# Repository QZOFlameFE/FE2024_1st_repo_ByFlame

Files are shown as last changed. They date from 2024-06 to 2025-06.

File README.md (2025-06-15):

<!-- 
<table>
<tr>
<th width=250>
CONTENT
</th>
</tr>
</table>
-->

<div style="display: flex; flex-direction: column; align-items: center; justify-content: center;"
-webkit-background-clip: text;
-webkit-text-fill-color: transparent;">
<h1 align = center> Future Engineers 2025 </h1>
<h2 align = center> Team name: QYZYLORDA Flame </h2>
<h2 align = center> Team members: Sadu Yernur, Bizhanuly Aidar </h2>
<h2 align = center> email: qzo.flame.fe2024@gmail.com </h2>
<div style="display: flex; flex-direction: column; align-items: center; justify-content: center;"
-webkit-background-clip: text;
-webkit-text-fill-color: transparent;">
<div align = center>
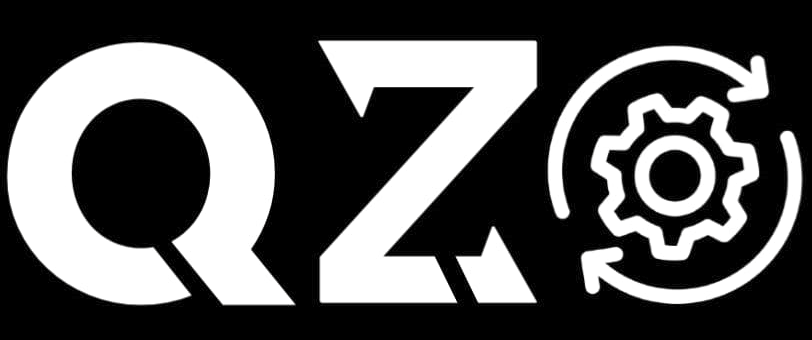
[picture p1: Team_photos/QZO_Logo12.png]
   
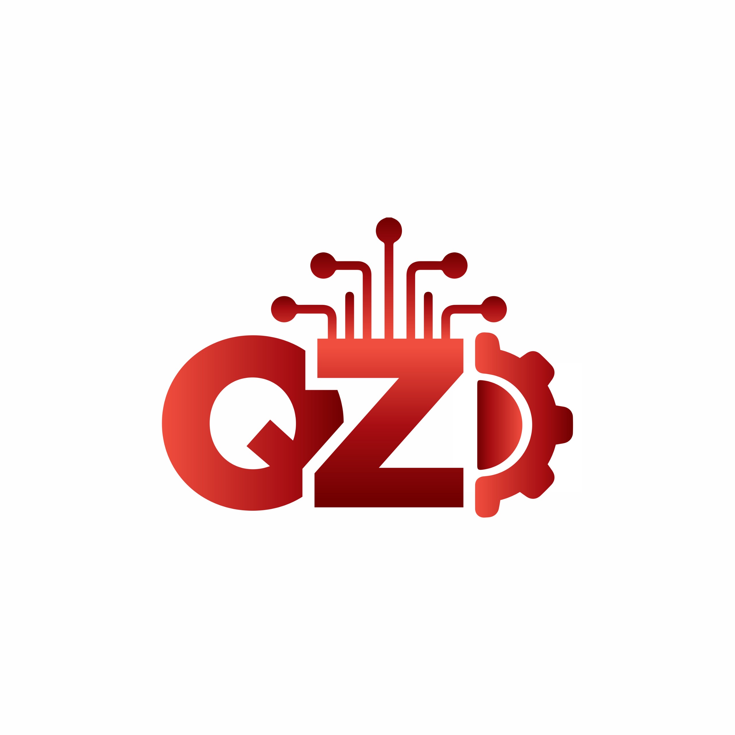
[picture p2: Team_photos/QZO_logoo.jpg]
  
</div>
</div>
</div>
<h2 align = center> Our team already participated in the last 2024 season and we won second place in FE category</h2>
<div align = center>
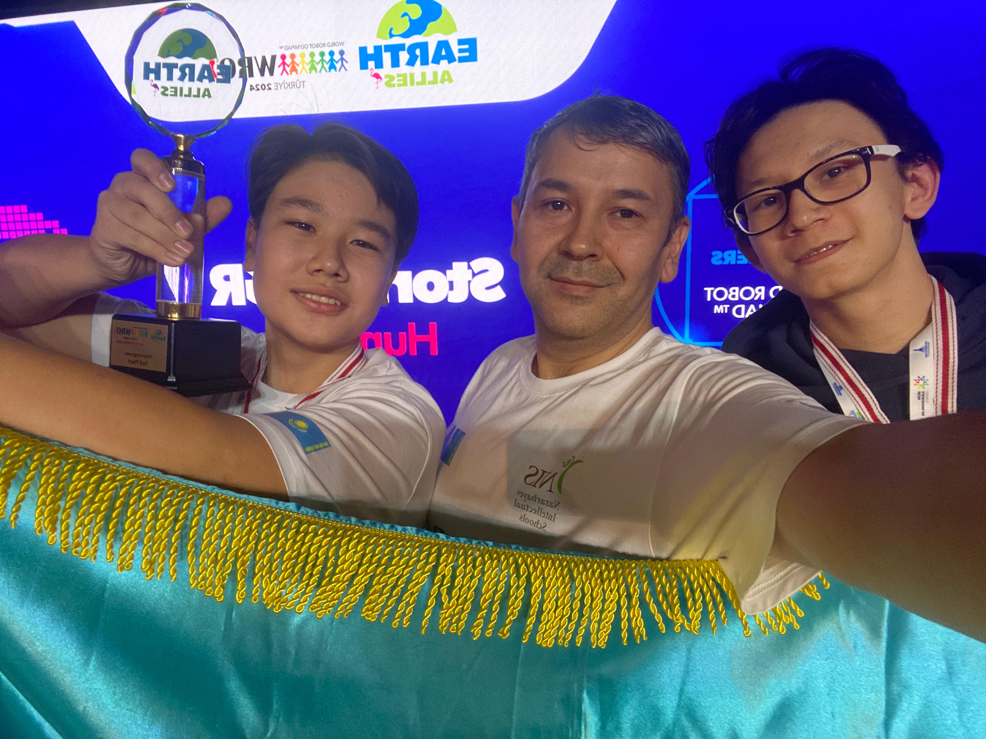
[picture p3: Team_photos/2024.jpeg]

</div>

# Contents 
* [**Mobility management**](#mobility-management)
  * [Chassis design and differential](#chassis-design-and-differential)
  * [Weight distribution](#weight-distribution)
  * [Camera position](#camera-position)
  * [Motor selection](#motor-selection)
* [**Power and sense management**](#power-and-sense-management)
  * [Power management](#power-management)
  * [Sense management](#sense-management)
* [**Obstacle management**](#obstacle-management)
  * [Change of the driving direction](#change-of-the-driving-direction)
  * [Parking pasition](#parking-position)
* [**Pictures**](#pictures)
  * [Robot Photos](#robot-photos)
  * [Team Photos](#team-photos)
* [**Performance videos**](#performance-videos)
* [**Code explanation**](#code-explanation)
* [**Conclusion**](#conclusion)
  * [Limitations](#limitations)
  * [Sugestions for further development](#sugestions-for-further-development)
# <hr/>
<!-- 

-->
# Mobility Management

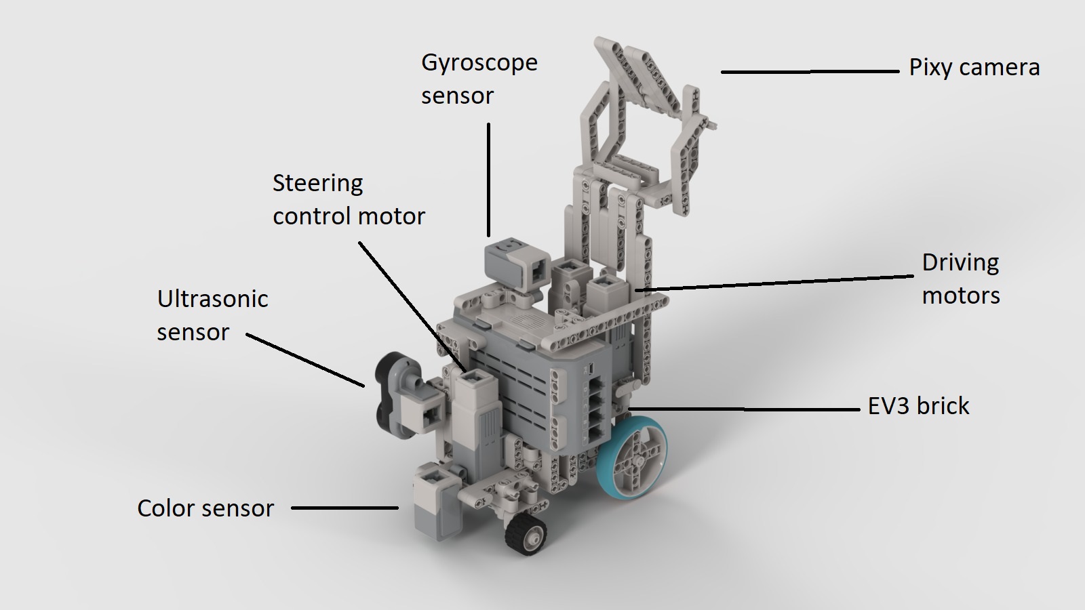
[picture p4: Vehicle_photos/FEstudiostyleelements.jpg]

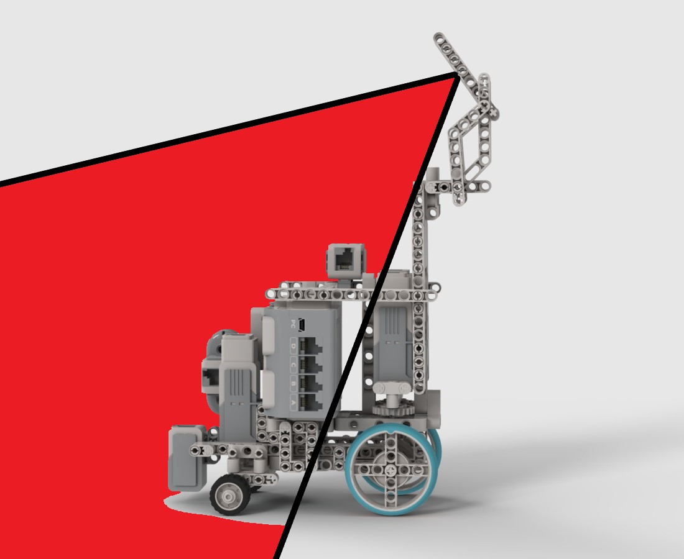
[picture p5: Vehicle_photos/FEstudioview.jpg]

<p>   Our robot is designed by lego, especially we used LEGO MINDSTORMS Education Core Set(Serial number 45544) and other LEGO EV3 sets: EV3 Expansion Set, EV3 Homeschool Combo Pack and others. You can view all of the LEGO EV3 sets by this link: <a href="https://www.bricklink.com/catalogList.asp?catType=S&catString=166.59.800">https://www.bricklink.com/catalogList.asp?catType=S&catString=166.59.800</a>. Robot's wheels are taken from LEGO SPIKE Prime set and its expansion set(serial numbers 45678-1 and  45680-1). </p> </br>
  
<p>   For better stability we used differential with two motors at the rear axle and steering control as required in the rules, our robot's size is 19.5cm (length); 13.5cm(width) and 27cm(height). We constructed the robot as small as possible, so its projection doesn't interfere during parking. </p>

<div align=center>
<table>
<tr>
<th width=250>
  
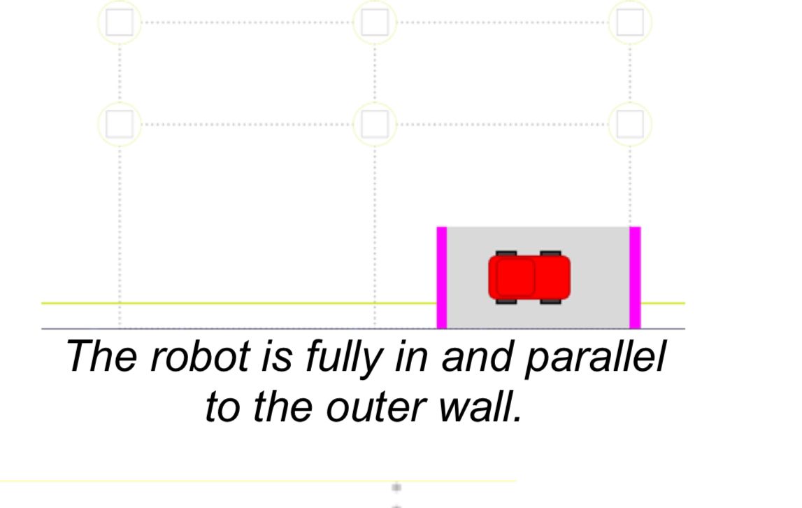
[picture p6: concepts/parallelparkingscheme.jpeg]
 </br>
</th>
</tr>
</table>
</div>

### Chassis design and differential
The base of our chassis design comes from Ackerman steering model geometry. It improves maintainabiity of the robot as it controls the smoothness of the turns because of the maximum degrees of the steering can move
We have a differential in driving rear axle of our robot to make turns smoother. If robot turns one wheel will move slower than second and it reduces radius of the turn so our robot turn is controlled by 2 mechanisms: steering mechanism and differential.
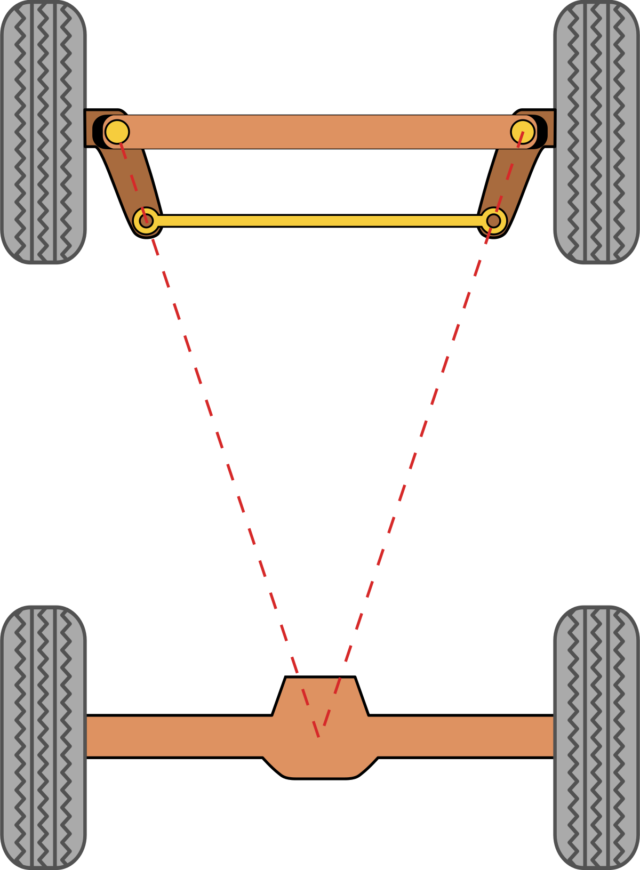
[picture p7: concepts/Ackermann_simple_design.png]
Ackermann Design

### Weight distribution
  As our robot is a self-driving car with steering mechanism and differential in rear axle we need to make our robot slight heavy, and distribute weight a bit behind the center of our robot to prevent the wheels from slipping. The slipping of the wheels in rear axle impacts our odometry and the programm.Also, we placed the EV3 P-Brick in the center of the robot to distribute the weight evenly, as the brick is a relatively heavy component(275g). Pixy camera is located quite behind the robot,that's why it don't maintain balance. To maintain balance, we used metal balls(you can see from instruction of our robot) from the Lego set and placed them in front of the robot. This way, we avoid the robot from wobbling.
  
### Camera position
  Our camera places as much higher(28cm) and behind(7cm from center of the robot) as its possible for better view and obstacle control. It also inclined a bit down to view blocks that are close to robot and limit the view for better obstacle management. Also we use additional motor to rotate camera to the robot and so decrease the length of the robot in the end to full-park.   
</div>

### Gyro sensor PD regulator and turns, angular rotation
LEGO EV3 Gyro Sensor is used to measure the angular rotation of the robot, allowing precise detection of turns. This data is fed into a PD regulator (Proportional-Derivative regulator), which ensures smoother control during turns, such as achieving an exact 90-degree rotation.  Change in the PD coefficients with dependence to the steering and its PID regulator enhances the robot’s maneuverability. Additionally, the gyro sensor is a significant part in the robot’s odometry system, providing opportunities to track its orientation and improve overall navigation accuracy.

### Steering control
The PID regulator controls the steering mechanism by setting a specific variable called “aim”, which represents the target position or direction. The PID controller is used to set the steering motor encoder and compare its current position to the value of “aim.” Based on this comparison, the PID algorithm sets the motor’s movement to smoothly align the steering mechanism with the desired direction. This ensures precise and stable control over the robot’s steering, allowing it to maintain accurate and smooth maneuvers during operation.

### Bypassing obstacles
The Pixy camera is used to detect obstacles and it captures visual data like X and Y coordinates, signature and processes it to identify objects. Once an obstacle is detected, the camera's data used to manipulate robot’s steering system. By specific formula that uses 3 parameters(signature, X and Y coordinate) values are setted and then transmitted to PID regulator of steering mechanism by setting proportional, integral, and derivative values to smoothly navigate around the obstacles. This approach allows the robot to bypass obstacles in real-time, improving its mobility and efficiency in dynamically.

### Aligning robot to the center
Odometry is utilized to align the robot to the center by combining the Gyro sensor’s PD regulator and odometry coordinates. A new PD regulator ensures smooth and precise alignment. This process corrects the robot’s position and orientation relative to the centerline straightforward zones. Aligning to the center is crucial because it compensates for the Pixy camera’s limited view angle, ensuring that the camera accurately detects obstacles or paths ahead. This alignment improves the robot’s navigation accuracy and stability during operation and improves Pixy camera's view angle so it can always detect the objects and view it.

### Motor selection
  We have a choice between 2 types of LEGO motors: large motor and medium motor, the large motor is powerful but the speed is lower, the medium motor is not that powerful but have a great speed. The comparison can be viewed by this link: <a href="https://www.eurobricks.com/forum/index.php?/forums/topic/87670-ev3-large-and-medium-motors-comparison/">https://www.eurobricks.com/forum/index.php?/forums/topic/87670-ev3-large-and-medium-motors-comparison/</a>. According to <a href="https://www.researchgate.net/publication/345182894_Dynamic_analysis_modeling_and_control_of_the_LEGO_EV3_modular_mobile_platform">research:</a> 

* Large servo motor (actuator) - maximum operating speed of 170 rpm, torque of 0.2 Nm and stopping torque of 0.4 Nm. It is positioned in the engine case an integrated encoder, a rotation meter, whose step is 1 degree of rotation and least sampling time 0.001 s.Also the power and speed is regulated by gear wheels and the size of the wheels. We choosed smaller wheels in steering mechanism because they do not move the robot, the only moves its trajectory.
* Medium-size servo motor - maximum speed of 250 rpm, running torque 0.08 Nm and stopping torque of 0.12 Nm, also with integrated encoder, identical to that of a large engine.
</br>
Also the wheels have low coefficient of friction to avoid loss of energy, but for wheels in the rear axles it will be better to choose wheels with a bit high cofficient of friction to avoid slipping of wheels. The rear wheels are bigger than wheels in front axle to have a better stability, movement control and the speed. It will be better to choose little smaller rear wheels than our. 
</br>
  The explanation of our construction design is on our youtube channel <a href="https://www.youtube.com/channel/UC0_5yZ2aPdJc0X5wtIw4ZcA">"QZO Flame" (tag: @QZOFlame)</a>.
   
   * [Building Instructions and BOM](https://github.com/QZOFlameFE/FE2024_1st_repo_ByFlame/blob/main/Instructions/Builiding_Instructions/README.md)
   * [3D model of Pixy Camera_Case](https://github.com/QZOFlameFE/FE2024_1st_repo_ByFlame/blob/main/3D_models/README.md) <br> (used application AutoCAD)
# <hr/>

# Power and sense management 

</br>

## Power management

</br>

  The core of our robot is <a href="https://pybricks.com/ev3-micropython/startbrick.html">EV3 Programmable Brick</a>, the power comes from a rechargable 10V Lithium Battery. EV3 P-Brick have 4 ports for motors and 4 ports for sensors.  Power consumption of motors and sensors: <a href="https://www.dexterindustries.com/ev3-current-consumption-measurement/">https://www.dexterindustries.com/ev3-current-consumption-measurement/</a>.
  <table>
<tr>
<th width=400>
  
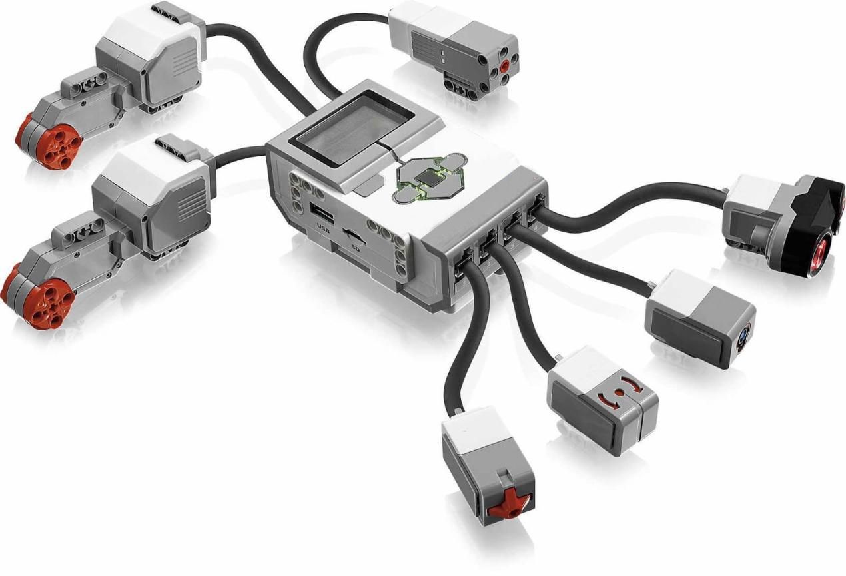
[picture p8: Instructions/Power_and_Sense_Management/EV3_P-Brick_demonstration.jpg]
EV3 with ports for sensors and motors
  
</th>
</tr>
</table>

  * [Electroschemes/wiring diagrams](https://github.com/QZOFlameFE/FE2024_1st_repo_ByFlame/blob/main/schemes/README.md)

    ## Why did we choose EV3 P-Brick?
    <ul>
    <li font size="10">EASY TO USE</li> <br>
    The EV3 comes with graphical programming environment (LEGO Mindstorms EV3 software), and it makes it much easier. This visual approach is more accessible than writing code in languages like C++ (Arduino) or Python (Raspberry Pi).<br> <br><br>
    <li>INTEGRATED HARDWARE</li> <br>
    EV3 comes with specialized LEGO motors and sensors (like color, infrared, and gyro), which are easy to connect and calibrate.<br> <br><br>
    <li>PORTABILITY</li>
    <br>
    EV3 is more portable and compact,because it is designed for easy handling, and its components are built with the purpose of being assembled and taken apart for quick project changes. <br> <br><br>
 
  ### EV3 P-Brick Energy distribution
  EV3 P-Brick have 4 ports for sensors and motors and all of them distributes and contributes most of the energy resources. While LEGO sensors contribute as much energy as they need by built-in control systems and framework abilities, varying between number of iteration per second, energy consumption and framework and IDE's abilities to proceed amount of data. Then the motors energy distribution is often regulated by control algorythms and values given in the programm, consequentlyleading to smart energy distribution to provide enough power and maintain accuratte readings without overloading.
  
  ### Monitoring features and flexibilty
  The LEGO EV3 power management system improves flexibility and efficiency through its convenient monitoring features and adaptable power options. The system supports multiple configurations, such as rechargeable lithium-ion batteries or standard AA batteries, providing a choice between them, also it is easier to change between batteries in LEGO because of real-time battery monitoring system that enables active energy management, providing alerts for low power and ensuring uninterrupted operation. This flexibility is further enhanced by integration with external power sources for extended runtime, while the monitoring features ensure optimal performance and safe components during tasks.
  
  ### Comparison with other popular controllers
  
  <table>
    <tr>
      <th width=33%>
        
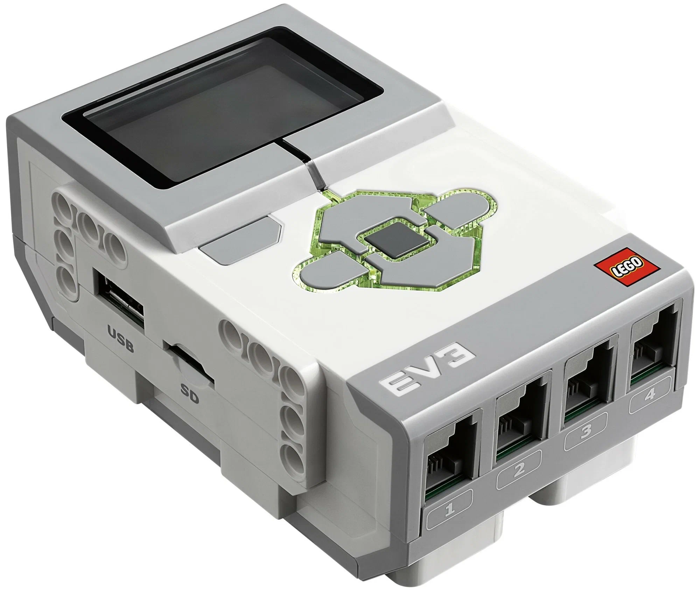
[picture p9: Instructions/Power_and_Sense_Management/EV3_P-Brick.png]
  
  
  EV3 P-Brick </th>
      <th width=33%>
        
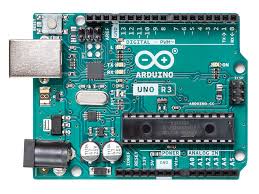
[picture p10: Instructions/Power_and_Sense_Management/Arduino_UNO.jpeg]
  
        
  Arduino UNO 
      </th>
      <th width=33%> 
      
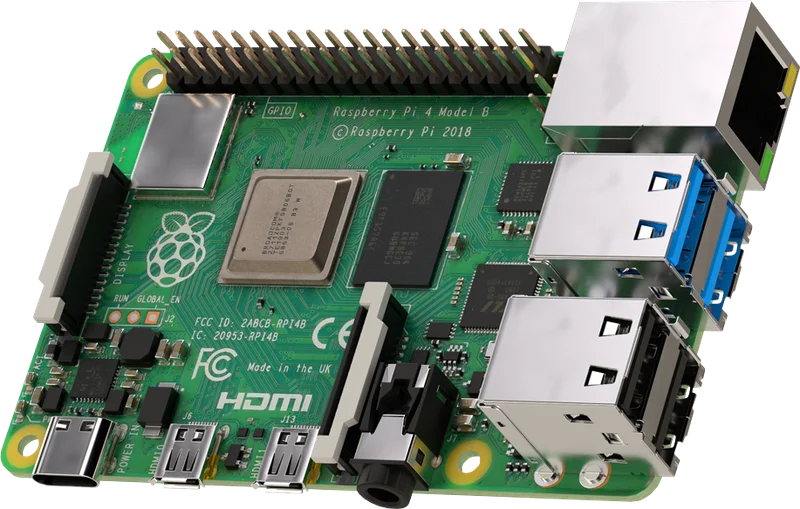
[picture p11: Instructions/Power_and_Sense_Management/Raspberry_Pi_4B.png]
  
       
  Raspberry Pi </th>
    </tr> 
    <tr>
    <td colspan=3 align=center> processor </td>
    </tr>
    <tr>
      <td align=center> 300 MHz, 1 core </td>
      <td align=center> 16MHz </td>
      <td align=center> 1.5 GHz, 4 cores </td>
    </tr>
     <tr>
    <td colspan=3 align=center> ports </td>
    </tr>
    <tr>
      <td align=center> 4 ports for sensors, 4 ports for motors </td>
      <td align=center> 14 digital, 6 analog pins </td>
      <td align=center> 40 GPIO pins </td>
    </tr>
    <tr>
    <td colspan=3 align=center> programming </td>
    </tr>
    <tr>
      <td align=center> LEGO Mindstorms, limited Python and C++ </td>
      <td align=center> Arduino IDE (C, C++ based) </td>
      <td align=center> Multiple languages (Python, C++, Java, etc.) </td>
    </tr>
  </table>
  </br>
  </br>
  
## Sense management 

</br>
  UART sensors of LEGO EDUCATION MINDSTORMS EV3 Core Set such as color, ultrasonic and gyro sensors are used for sense management of our robot. </br>
  Gyro sensor is used to save initial robot position in degrees and count the deviation from it. Ultrasonic sensor measures the distance from robot to wall. Color sensor is used to know the driving direction of the round. Encoders in medium motors are used to know the distance that robot moved. Our programm uses mix of this sensors to create the odometry of our robot, by the usage of encoders, gyro sensor and Pythagoras theorem we calculate the displacement that robot moves from initial positions and convert it to x and y coordinates. Before the first line in first lap the odometry is relative to the robot's initial position and after the color sensor views the line it recognizes robot direction and by specific math formulas it converts relative odometry to full odometry of the map, the center of the map is the center of odometry where x and y coordinates are equal to zero. Ultrasonic sensor and Gyro sensor in combine used to fix odometry also by Pythagoras theorem and exceptions for the situations when ultrasonic sensor view blocks. The detailed info is given by this links related to each sensor's purpose.
  
  * [color sensor](https://github.com/QZOFlameFE/FE2024_1st_repo_ByFlame/blob/main/Instructions/Power_and_Sense_Management/color_sensor.md)
  * [ultrasonic sensor](https://github.com/QZOFlameFE/FE2024_1st_repo_ByFlame/blob/main/Instructions/Power_and_Sense_Management/ultrasonic_sensor.md)
  * [gyro sensor](https://github.com/QZOFlameFE/FE2024_1st_repo_ByFlame/blob/main/Instructions/Power_and_Sense_Management/gyro_sensor.md)
  * [encoders from motors](https://github.com/QZOFlameFE/FE2024_1st_repo_ByFlame/blob/main/Instructions/Power_and_Sense_Management/encoders_from_motors.md)
  * [odometry](https://github.com/QZOFlameFE/FE2024_1st_repo_ByFlame/blob/main/Instructions/Power_and_Sense_Management/odometry.md)
# <hr/>
<!-- 

-->
# Obstacle management
  For the obstacle detection we used Pixy2 camera and PixyMon v2 application to configure it. To use it in LEGO MINDSTORMS application you need to install special library. All of the downloads are able in official site of Pixy2 <a href="https://pixycam.com/downloads-pixy2/">https://pixycam.com/downloads-pixy2/</a>.We get x y coordinates from the Pixy camera by placing the robot on two points along the correct trajectory of robot (If the pillar is red, it should go around on the right, if it is green, on the left).From the obtained value (x,y coordinates) we calculate a quadratic function by two points (you can calculate it by the link:) <a href="https://planetcalc.com/8110/?language_select=en&ysclid=m0a3s77i4p794636345">linear function by two points. Every straightforward section has its own coordinate center and 6  possible locations of pillars. Robot changes its odometry coordinate when he passes second line(blue or orange, depends on a direction). Corner sections do not include odometry system.</a>
  </br> </br>
<table>
<tr>
<th width=500>
  
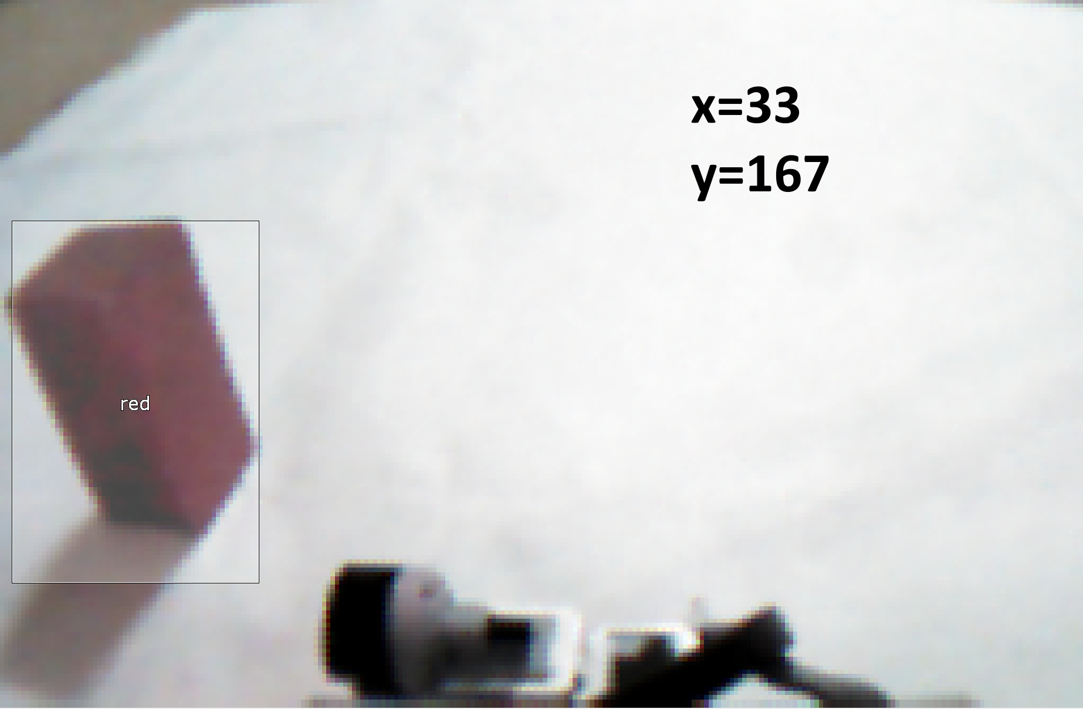
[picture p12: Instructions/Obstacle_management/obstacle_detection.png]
obstacle detection
  
</th>
  <th width=500>
    
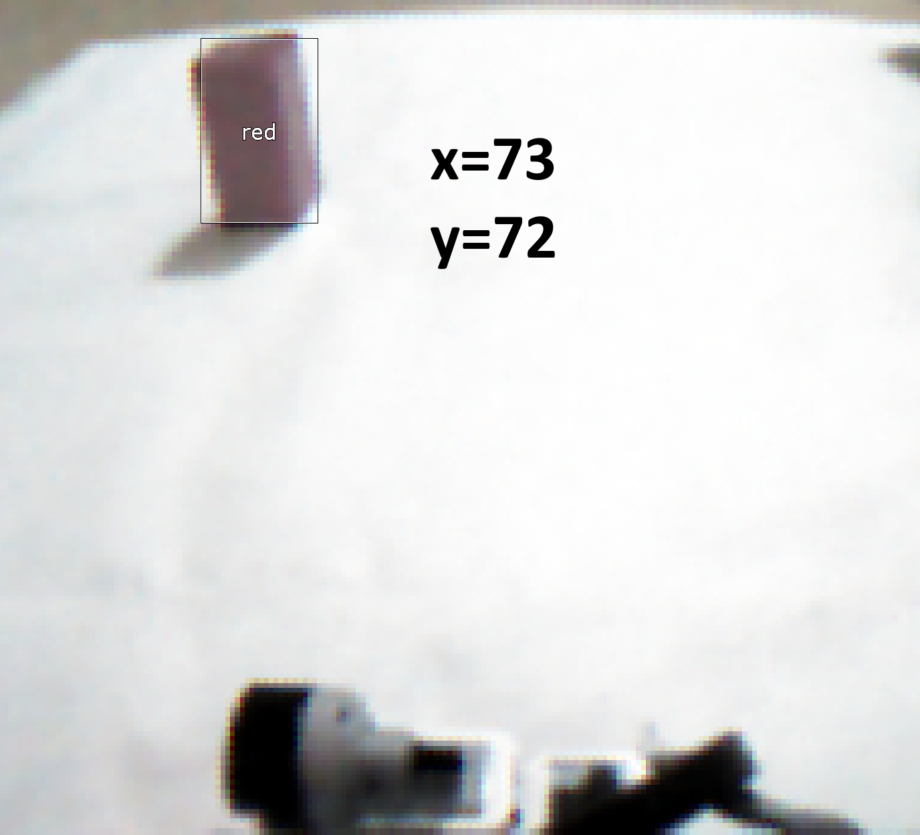
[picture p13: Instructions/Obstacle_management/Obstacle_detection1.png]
obstacle detection
  
  </th>
  <tr>
    <th width=500>
      
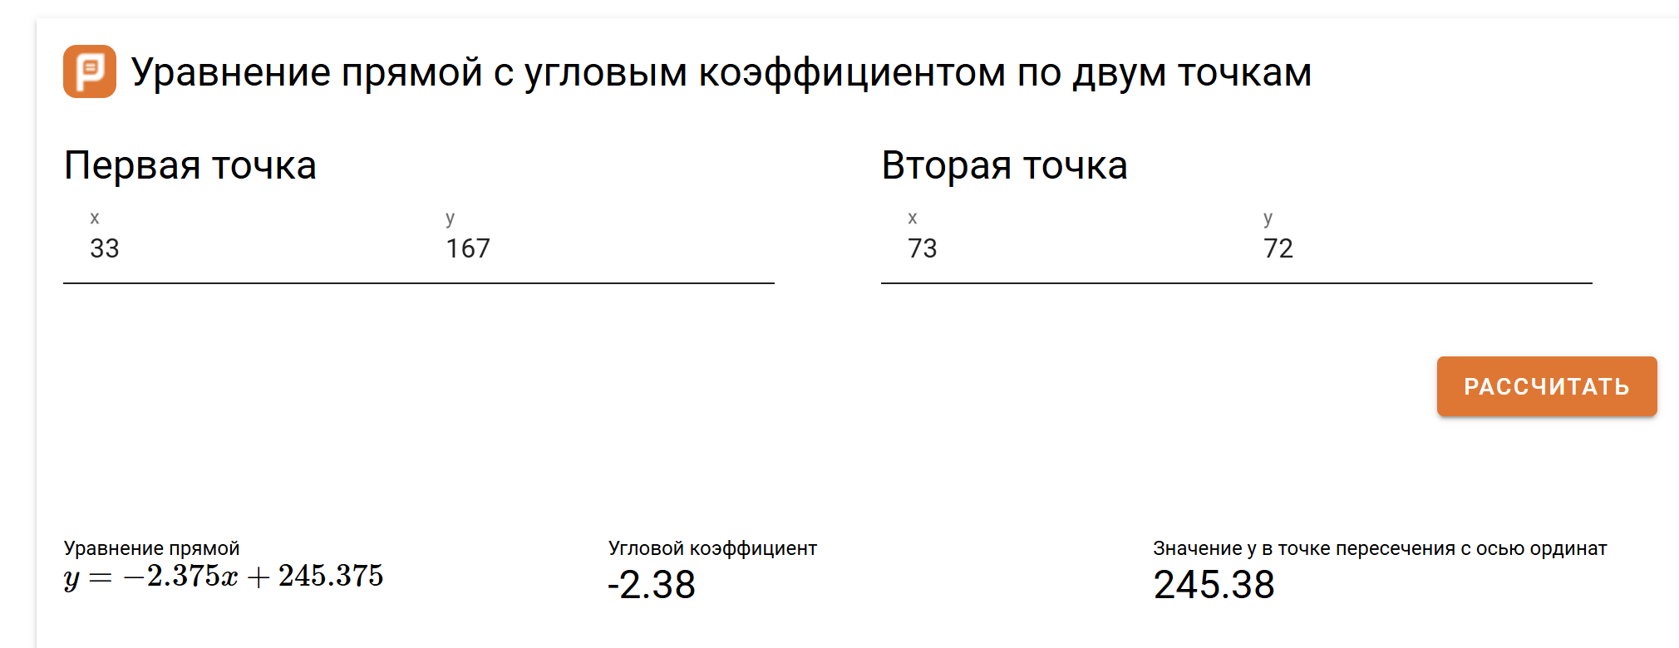
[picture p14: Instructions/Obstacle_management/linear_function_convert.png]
linear function
  
</th>
  <th width=500>
    
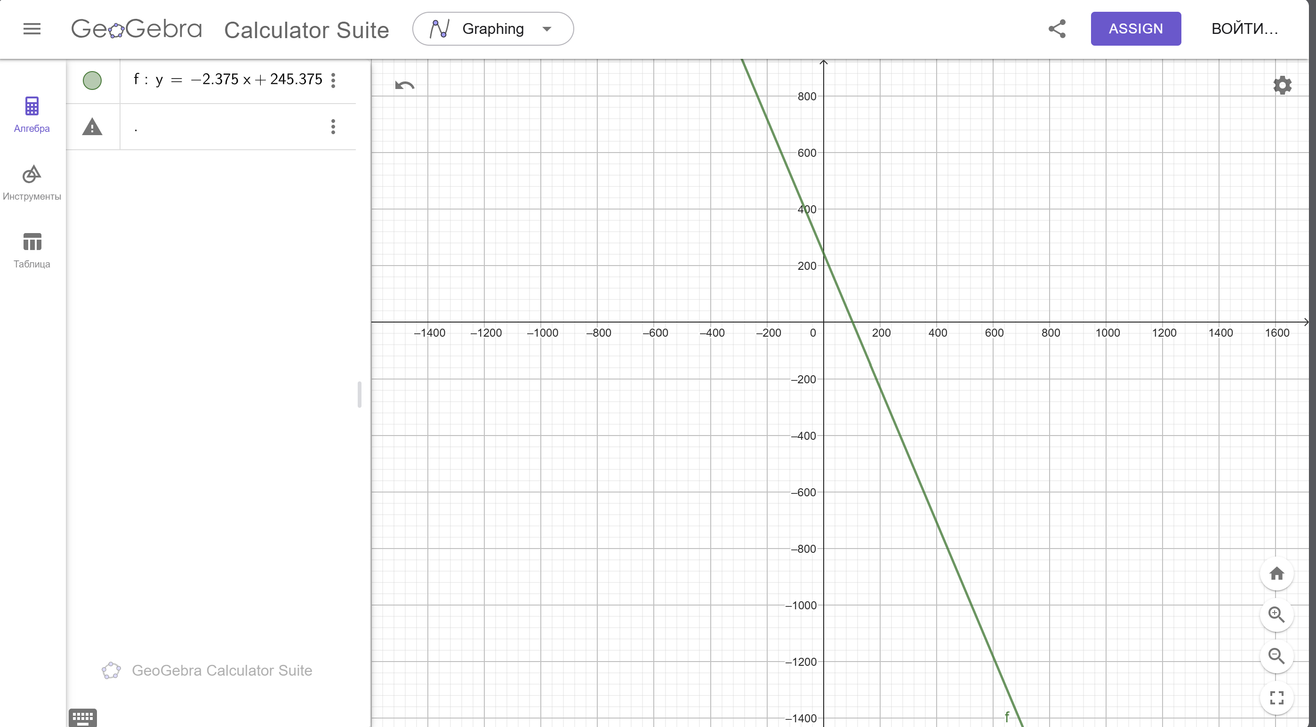
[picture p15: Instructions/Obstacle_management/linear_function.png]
linear function
  
</table>

</br>
<div align = center style="display: flex; flex-direction: column; align-items: center; justify-content: center; color: gray">

<table>
<tr>
<th width=250>
  
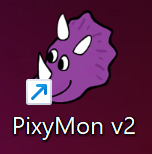
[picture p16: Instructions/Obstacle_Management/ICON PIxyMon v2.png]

<p> 
PixyMon v2 application
</p>
</th>
</tr>
</table>

<table>
<tr>
<th width=400>

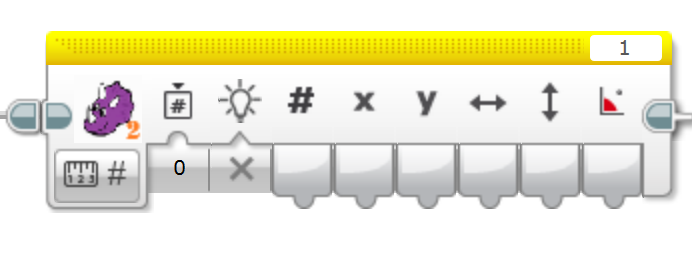
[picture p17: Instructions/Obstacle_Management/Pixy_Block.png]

<p>
Pixy block for LEGO MINDSTORMS
</p>
</th>
</tr>
</table>

Pixy2 camera is a universal tool as it can work with EV3, arduino and raspberry. </br>
<table>
<tr>
<th width=250>
  
Pixy camera
<p> 
Pixy camera
</p>
</th>
</tr>
</table>
</div>

For the work in LEGO MINDSTORMS application you need to install "pixy block".<br>
This block outputs: </br>
<ol>
<li>Signature id with the highest value of y coordinate </li>
<li>camera's relative x coordinate of the object </li>
<li>camera's relative y coordinate of the object </li>
<li>relative width of the object</li>
<li>relative height of the object </li>
<li>angle of the object to camera </li>
<table>
<tr>
<th width=400>
  
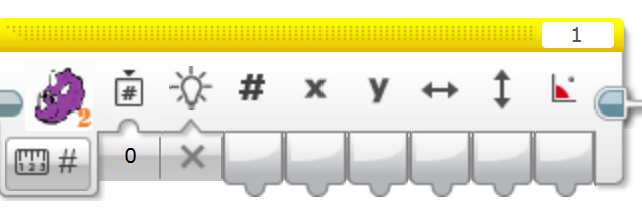
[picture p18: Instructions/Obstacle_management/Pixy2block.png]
Pixy2 block

</th>
</tr>
</table>

## Automatic control
The robot's trajectory is determined by two main situations: <br>
<ul>
  <li>
    when pixy camera sees a road sign
  </li>
  <li>
    when pixy camera does not see road sign
  </li>
</ul> <br>

### Bypassing obstacles (when pixy camera sees a road sign)
We use steering mechanism and pixy2 coordinates and connect them with linear function. Y value from pixy2 gives how far the robot should be from the object, using a quadtratic function. Using the obtained value and the real value X from pixy2, we can find an error between robot and pillar and give this error to the steering mechanism. So if the pillar is close to robot linear function gives high values to steering mechanism's motor in order to avoid crush. <br>

https://github.com/user-attachments/assets/eb8f1eea-5bec-42ee-9bcd-57115f89046b
### Align center (when pixy camera does not see road sign)
Our robot aligns itself with the center of the road when it doesn't see an object, so as not to crash into parking spaces or miss a road sign. To center the robot, it uses odometry. The module x coordinate of the center of the road is equal to 25 (x is 25 or -25) because the robot uses segmented odometry (the center coordinate (0;0) is the center of the every straightforward section) <br>
<table>
<tr>
<th width=250>
  

<p> 
Segmented odometry
</p>
</th>
</tr>
</table>
</div>
It determines the error between the coordinate of the robot and the center of the road and is given to the steering mechanism so that it aligns itself to the center thanks to the constant formula.

## Parking position

We use ultrasonic sensor for precise parking and we already know where parking zone is, because it is located in the section where we started, but since we only have one ultrasonic and in the clockwise run ultrasonic will be pointed to the inner wall, we will have to make turn. Robot will drive till it sees orange line and will turn and align near to the outer walls, so the parking process consists of 3 steps:
<ul>
  <li>drive till the orange</li>
  <li>turning back and aligning </li>
  <li> finding the exact location of the parking</li>
  <li>parallel parking</li>
</ul>
<br>

### Make a turn 
our robot makes a turn if the robot moves clockwise so that the ultrasonic looks at the outer border

### Search for a parking zone
Our robot should move parallel and close to the outer side until it sees the parking zone. To be close to parking is we also use pixy2 relative coordinates and odometry to know the parking zone's position. Counter clockwise run includes backward movement and it stops and moves forward at orange line. Pixy allows robot to not go too far from parking section. Clockwise run includes forward movement and 180 degrees turn when it sees orange.

### park in the zone
To park accurately, an ultrasonic sensor is used, when this sensor notices a parking wall, the robot stops and uses cycle of turning steering wheel right,left and moving back, forward on a short distance. 
<br>
<br>
*Most tasks are performed using a pixy camera, here you can see how to set up this camera*

  * [Pixy2 camera's configuration](https://github.com/QZOFlameFE/FE2024_1st_repo_ByFlame/blob/main/Instructions/Obstacle_management/README.md)

# <hr/>

# Pictures
### Robot photos

<table>
<tr>
  <th width=50%>

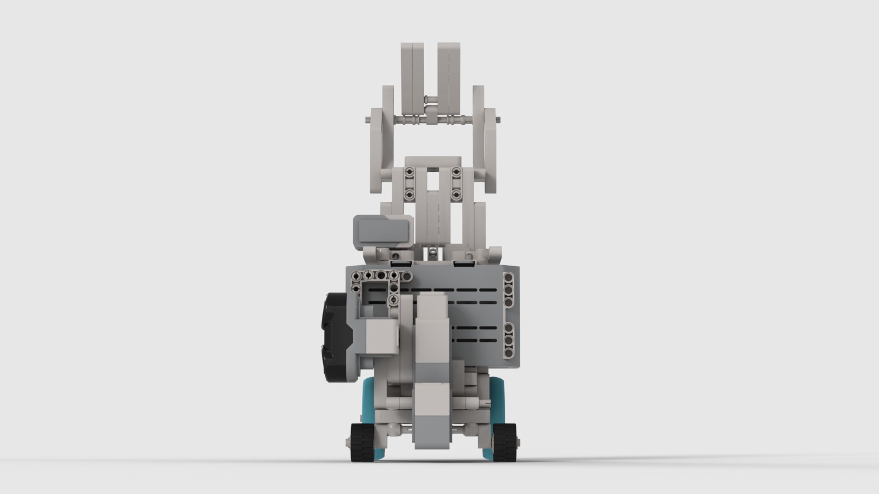
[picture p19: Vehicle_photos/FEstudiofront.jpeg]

  </th>
  <th width=50%>

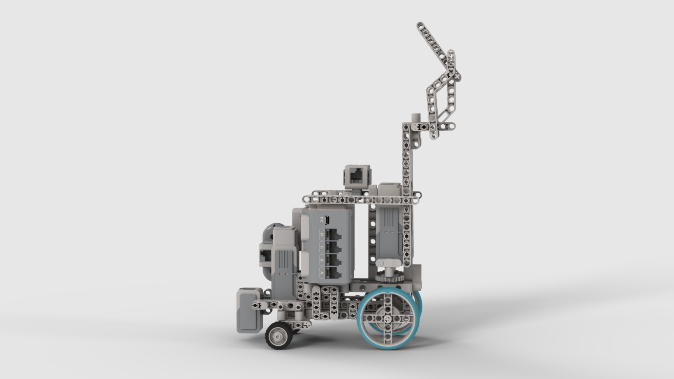
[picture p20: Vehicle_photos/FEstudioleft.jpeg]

  </th>
</tr>
<tr>
  <td width=50%>
    
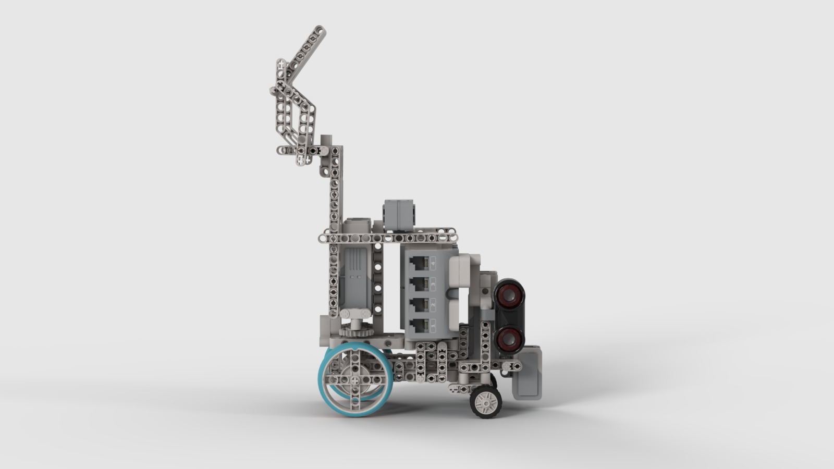
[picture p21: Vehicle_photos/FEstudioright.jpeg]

  </td>
  <td width=50%>

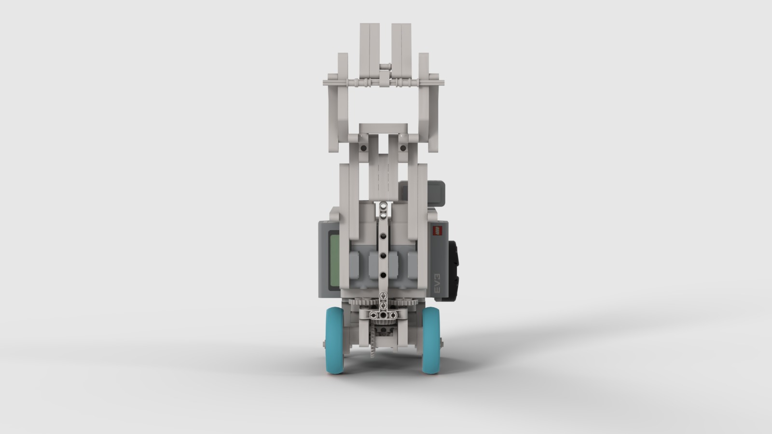
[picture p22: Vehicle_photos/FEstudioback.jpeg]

  </td>
</tr>
<tr>
  <td width=50%>

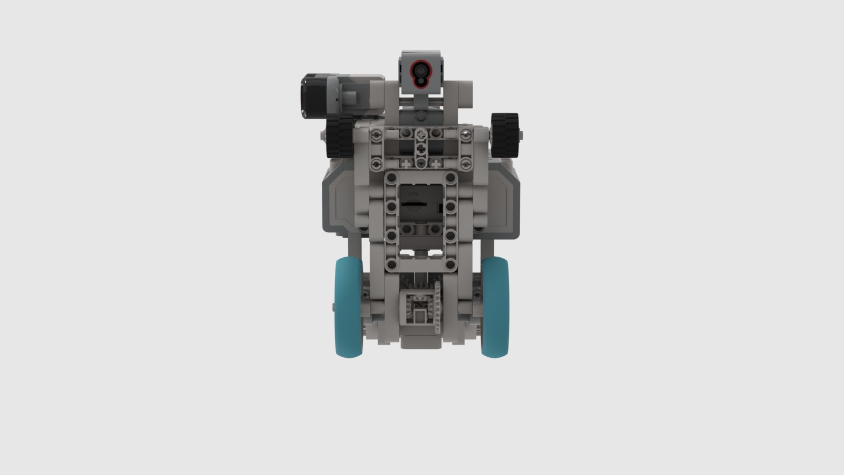
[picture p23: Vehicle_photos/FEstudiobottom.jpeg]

  </td>
  <td width=50%>

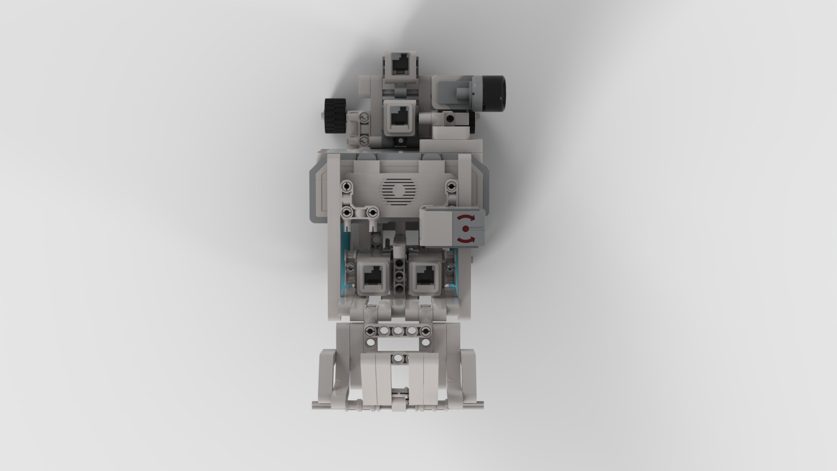
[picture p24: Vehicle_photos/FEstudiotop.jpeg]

  </td>
</tr>
<tr>
  <td width=50%>
  
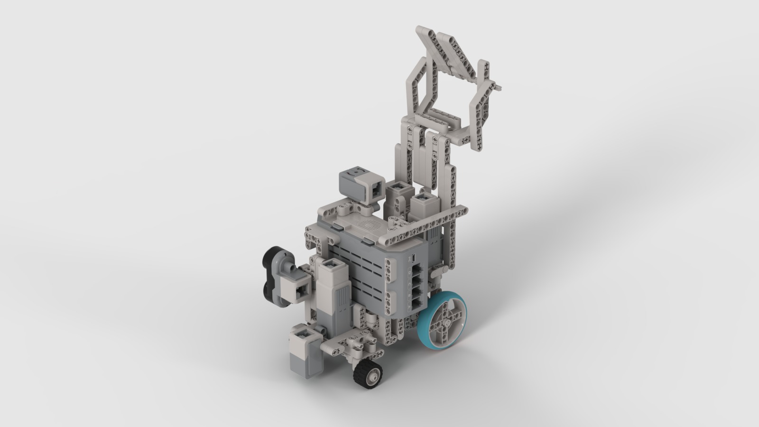
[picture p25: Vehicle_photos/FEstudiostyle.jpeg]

  </td>
  <td width=50%>
    
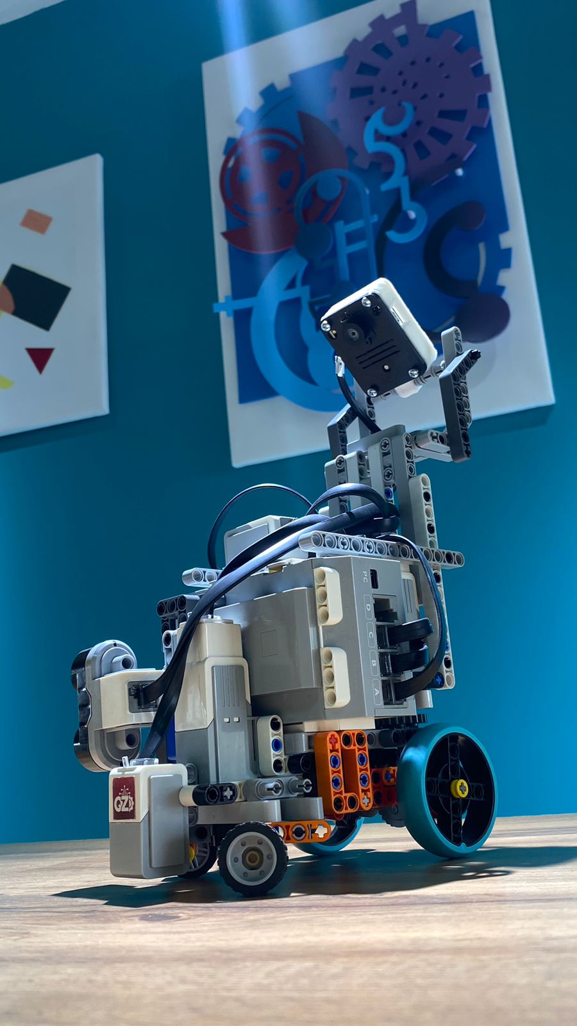
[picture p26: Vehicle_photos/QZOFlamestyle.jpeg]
  
    
  </td>
</tr>
<tr>
  <td width=50%>
    
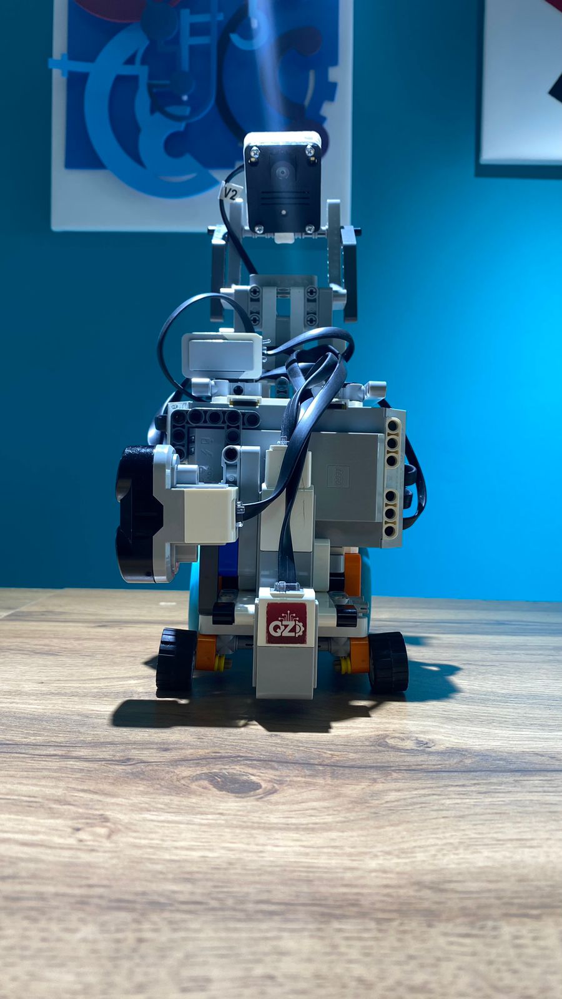
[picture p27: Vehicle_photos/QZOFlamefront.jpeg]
  
    
  </td>
  <td width=50%>
    
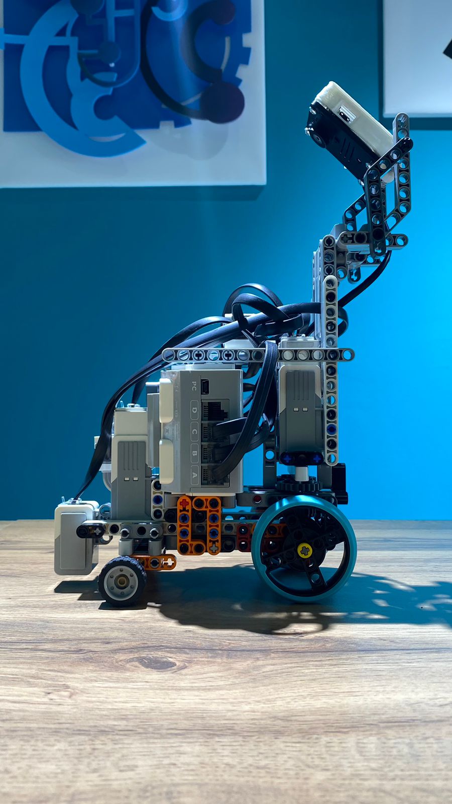
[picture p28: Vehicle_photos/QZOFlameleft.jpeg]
  
    
  </td>
</tr>
<tr>
  <td width=50%>
    
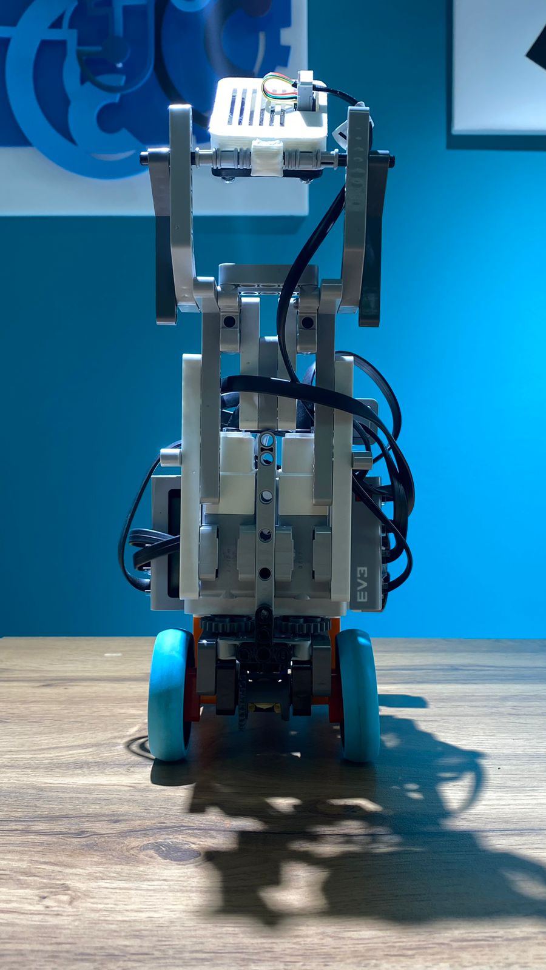
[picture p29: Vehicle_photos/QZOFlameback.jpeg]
  
    
  </td>
  <td width=50%>
    
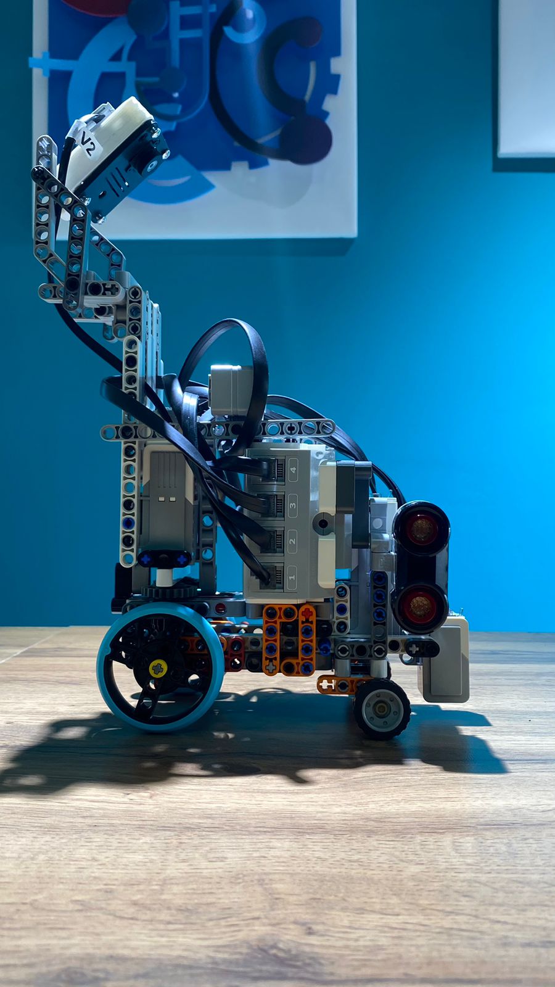
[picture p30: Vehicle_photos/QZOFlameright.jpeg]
  
    
  </td>
</tr>
<tr>
  <td width=50%>
    
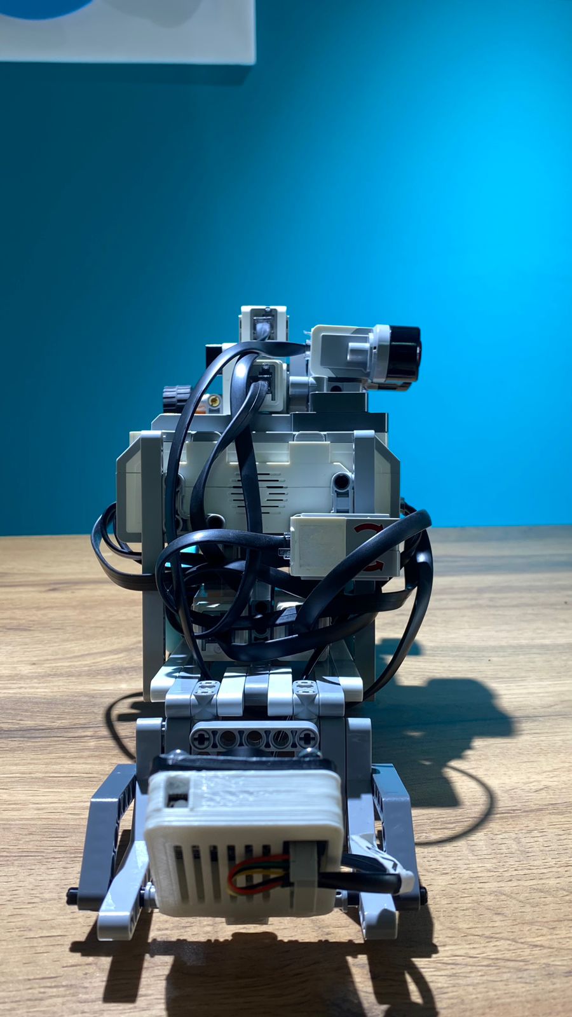
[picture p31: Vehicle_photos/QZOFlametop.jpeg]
  
    
  </td>
  <td width=50%>
    
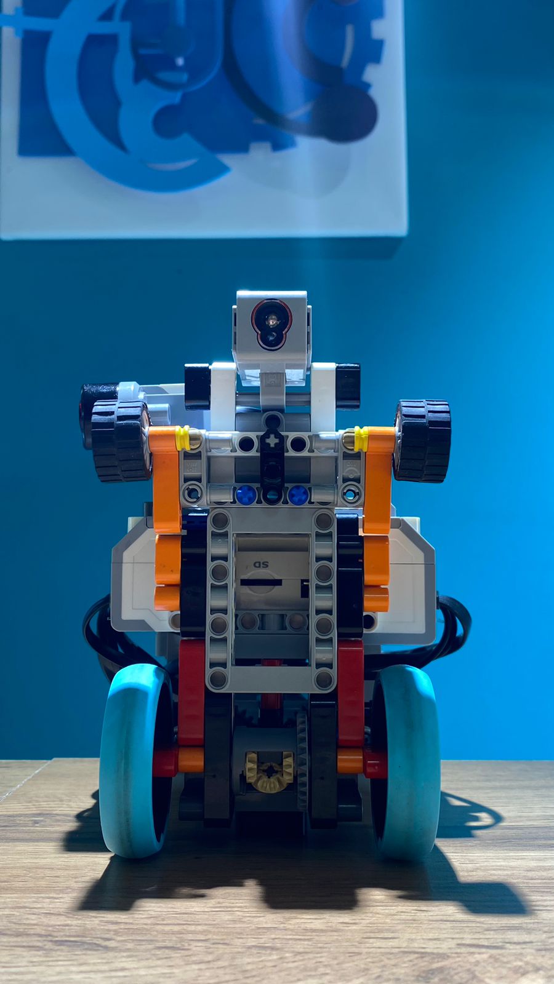
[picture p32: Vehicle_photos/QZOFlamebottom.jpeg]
  
    
  </td>
</tr>
</table>

## Team Photos
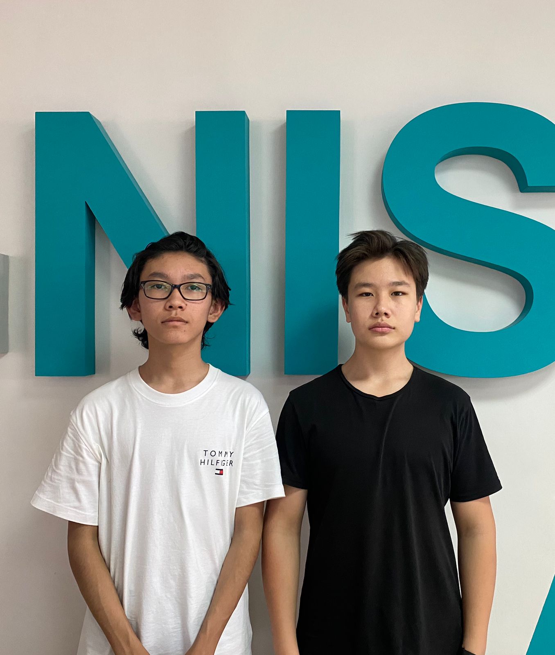
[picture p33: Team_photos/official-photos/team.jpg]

</br>
</br>
# <hr/>

<!-- 

-->
# Performance videos
### Open Challenge: https://www.youtube.com/watch?v=abwXTLdPtoA </br>
### Obstacle Challenge: https://youtu.be/TMfxzI9ZFoQ?si=zyM7kieHw5FU_5LX </br>
### Robot parts discussion: https://www.youtube.com/watch?v=4ONiXjtQosE </br>
# <hr/>

# Code explanation
The code is written in LEGO MINDSTORMS block programming language and you can download and check it 
<a href="https://github.com/QZOFlameFE/FE2024_1st_repo_ByFlame/blob/main/programms/Second%20version%20of%20programm.ev3">here</a>. </br> </br>

First of all we align the steering wheels to the center, so the robot moves straightforward. Then in configuration we set app all of the variables with specific values and using the bug of LEGO MINDSTORMS we reset the values of gyro sensor. Then our programm splits into 3 streams, first for robot control, 2nd for taking the values of Pixy2 camera into variables for obstacle management and the 3rd is for taking the values of UART sensors that are LEGO sensors and using the logic to determine the line color and round direction, activating the logic flag for turn, also the PID regulator of steering control is managed. Dividing the code into 3 streams is necessary for LEGO platform because it improves data processing and optimization of the programm logic and programm operating speed and improving precisesness of data. All of the key principles are in the 1st stream. This stream used for robot control and is responsible for the aligning to the center and to detour the obstacles. After that the main stream ends a loop for 3 laps and starts the parking.

# Conclusion
## Limitations

<table>
  <tr>
    <th align = center> Mobility Management </th>
    <td> 
    <ul>
      <li> LEGO motors, sensors and P-Brick are large in comparison with other electrical components </li>
      <li> LEGO EV3 set have limited opportunities like it is impossible to make Ackermann steering control geometry </li>
      <li> creating construction only by LEGO diminish </li>
    </ul>
    </td>
  </tr> 
    
  <tr>
    <th> Power and Sense Management </th>
    <td> <ul> 
      <li> 1 core CPU deprives multithreaded data processing and accuracy of sensor records. </li>
      <li> Only 4 ports for sensors and 4 ports for motors can be used. </li>
      <li> The Operating System of EV3 P-Brick is limited in functionality and flexibility. </li>
      <li> EV3 P-Brick have limited abilities in comparison with Raspberry Pi 4B that is a small computer. </li>
      <li> EV3 P-Brick is limited in source of motors and sensors since special firmware is needed for sensors and motors to interact with EV3 P-Brick. </li>
      <li> EV3 system has stopped in updates, and have some bugs like active bluetooth mode that sometimes interferes the operation of sensors </li> 
      <li> LEGO sensors are less accurate in comparison with other available sensors </li>
    </td>
  </tr>
      
  <tr>
    <th align = center> Obstacle Management </th>
    <td> <ul>
      <li> Pixy2 camera's quality is low (1.3 megapixels) </li>
      <li> Uses I2C that limits the sensor recordings to 60 times per second and lower </li>
      <li> Outputs only specified values </li>
      <li> Strong dependence on the lighting level </li>
    </td>
  </tr>
</table>

## Sugestions for further development
<!-- 
Since LEGO platform have numerous limitations it would be better to switch on Raspberry Pi's newest model. Raspberry Pi is a single board computer that affords the abilities to work with electronics. The main advantages by switching on Raspberry Pi would be the ability to use AI for detecting objects, using numerous and various sensors for better power and sense and obstacle managements. For the construction making it would be better to built own construction including the aspects of mechanical engineering, especially Ackermann Steering Geometry for smooth turns. Also it would be possible to make construction smaller and aerodynamic for better control and to fit into parking lot vertically as it is easier. Wheel selection is also an important factor, as better rubber on wheels prevents their slipping making the encoder values more accurate and improves traction. The smaller wheels for steering mechanism reduces the turn radius, and big wheels on rear axle improves the speed. Gears system regulates the torque and speed. For obstacle management choosing camera with greater resolution, better resistence to light changes and using AI technologies would improve the obtacle avoidance. Using more accurate sensors with more iterations per second would improve the sense management. Motors with more torque, RPM and damage resistance would improve the power and sense management. 
-->

<table>
  <tr>
    <th align = center> Switch control-board to Raspberry Pi </th>
    <td> 
      Since LEGO platform have numerous limitations it would be better to switch on Raspberry Pi's newest models. Moreover Raspberry Pi platform is considered as single board computer that includes all of the features of personal computers such as programming flexibility, better peripherals and ability to use AI
    </td>
  </tr> 

  <tr>
    <th>
      Mobility Management
    </th>
    <td>
      Switch on own designed details and improving aerodynamics, diminishing the size, creating great  Ackermann Steering Geometry for smooth turns. Switching the wheels such as smaller the wheels of steering mechanism the smoother are the turns and smaller the turn radius. Bigger wheels on rear axle improves the speed but reduces the torque, as well as gears mechanism the greater the speed, the smaller the torque. Also selection of wheels with better rubber will improve the traction and diminish slipping which is important for odometry base and sense management based on encoders. Also LEGO motors are fragile and can be easily damaged, so more strong motors with greater index of load condition will improve the stability of the robot.
    </td>
  </tr>
    
  <tr>
    <th> Power and Sense Management </th>
    <td> 
      Using more advanced sensors with greater accuracy level and greater number of iterations per second will improve the sense management and trajectory control. The same is for motor selection, greater speed, traction, torque and accuracy of encoder values are closely related to the motor.
    </td>
  </tr>
      
  <tr>
    <th align = center> Obstacle Management </th>
    <td> 
      Choosing camera with greater resolution, better resistence to light changes and using AI technologies would improve the obtacle detection and avoidance. 
    </td>
  </tr>
</table>

<!-- 

# Programm Logic
First of all we align the steering wheels to the center, so the robot moves straightforward. Then in configuration we set app all of the variables with specific values and using the bug of LEGO MINDSTORMS we reset the values of gyro sensor. Then our programm splits into 3 streams, first for robot control, 2nd for taking the values of Pixy2 camera into variables for obstacle management and the 3rd is for taking the values of UART sensors that are LEGO sensors and using the logic to determine the line color and round direction, activating the logic flag for turn, also the PID regulator of steering control is managed. Dividing the code into 3 streams is necessary for LEGO platform because ..... All of the key principles are in the 1st stream. This stream used for robot control and is responsible for the aligning to the center and to detour the obstacles. After that the main stream ends a loop for 3 laps and starts the parking.

## Programm analysis

-->
<!-- # Engineering Factor
### Construction making
  For our construction we used LEGO MINDSTORMS Education Set and wheels from LEGO SPIKE Prime Set as it conducts simple platform LEGO MINDSTORMS application for code, logic and powerful UART sensors as Gyro, Ultrasonic and Colorsensor for sense management and EV3 programmable brick as a main controller. </br>

  Pixy2 camera is a powerful tool with I2C communication protocol. It is used to distinguish colors of red, green blocks and parking in obstacle challenge, their position by relative coordinates and their relative sizes. It also has its own programm <u>PixyMon v2</u> for configuration of Pixy2 camera, with interactive interface including various settings. </br>
### Programming
  For the programming we used <a href="">LEGO MINDSTORMS</a> application. 
# <hr/>

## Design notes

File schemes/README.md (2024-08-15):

## Power
EV3 P-Brick: https://github.com/QZOFlameFE/FE2024_1st_repo_ByFlame/blob/main/schemes/95646c01%20Programmable%20brick.pdfd </br>
Rechargable Battery: https://github.com/QZOFlameFE/FE2024_1st_repo_ByFlame/blob/main/schemes/95656%20Rechargeable%20battery.pdf </br>
Medium motor: https://github.com/QZOFlameFE/FE2024_1st_repo_ByFlame/blob/main/schemes/99455%20Medium%20motor.pdf </br>
## Sensors
Color sensor: https://github.com/QZOFlameFE/FE2024_1st_repo_ByFlame/blob/main/schemes/95650%20Color%20sensor.pdf </br>
Ultrasonic sensor: https://github.com/QZOFlameFE/FE2024_1st_repo_ByFlame/blob/main/schemes/95652%20Ultrasonic%20sensor.pdf </br>
Gyro sensor: https://github.com/QZOFlameFE/FE2024_1st_repo_ByFlame/blob/main/schemes/99380%20Gyro%20sensor.pdf </br>
Pixy2 camera: https://github.com/QZOFlameFE/FE2024_1st_repo_ByFlame/blob/main/schemes/Pixy2.pdf </br>

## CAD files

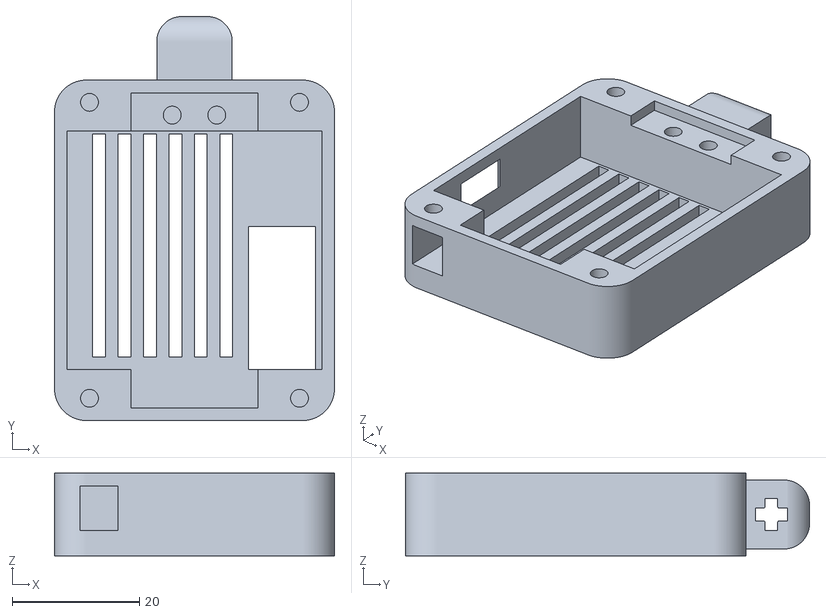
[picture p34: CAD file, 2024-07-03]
3D_models/PIXY_Case1.stl
44.0 x 63.5 x 13.0

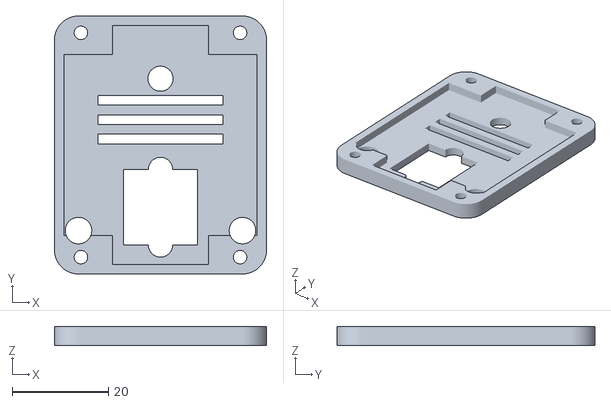
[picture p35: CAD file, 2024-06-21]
3D_models/PIXY_Case2.stl
44.0 x 53.5 x 4.00

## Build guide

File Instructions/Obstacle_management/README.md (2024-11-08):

<table>
<tr>
<th width=800>

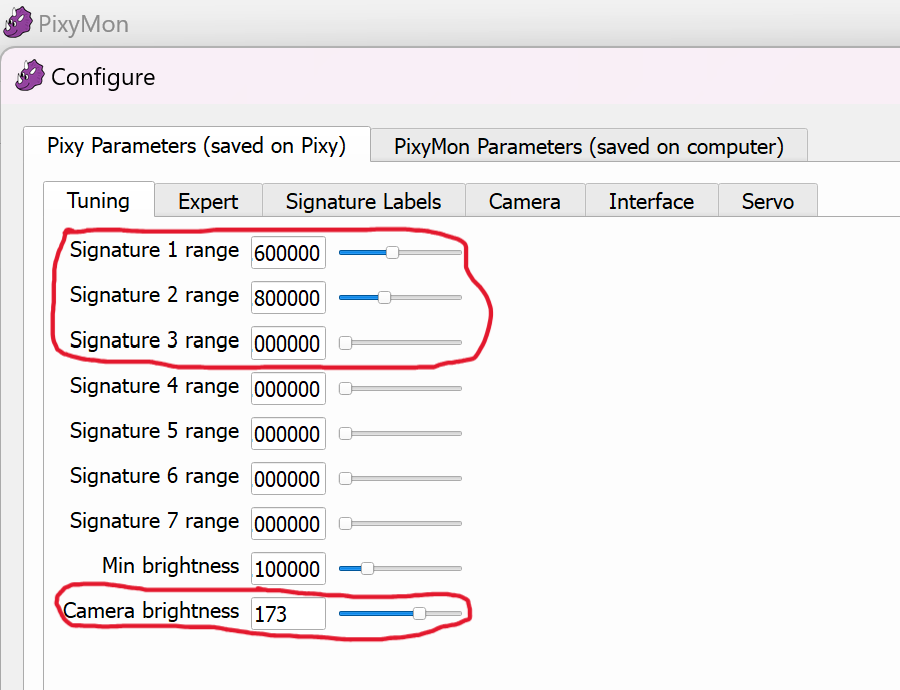
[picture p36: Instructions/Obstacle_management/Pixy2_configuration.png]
PixyMon configuration

</th>
</tr>
</table>

<table>
<tr>
<th width=800>

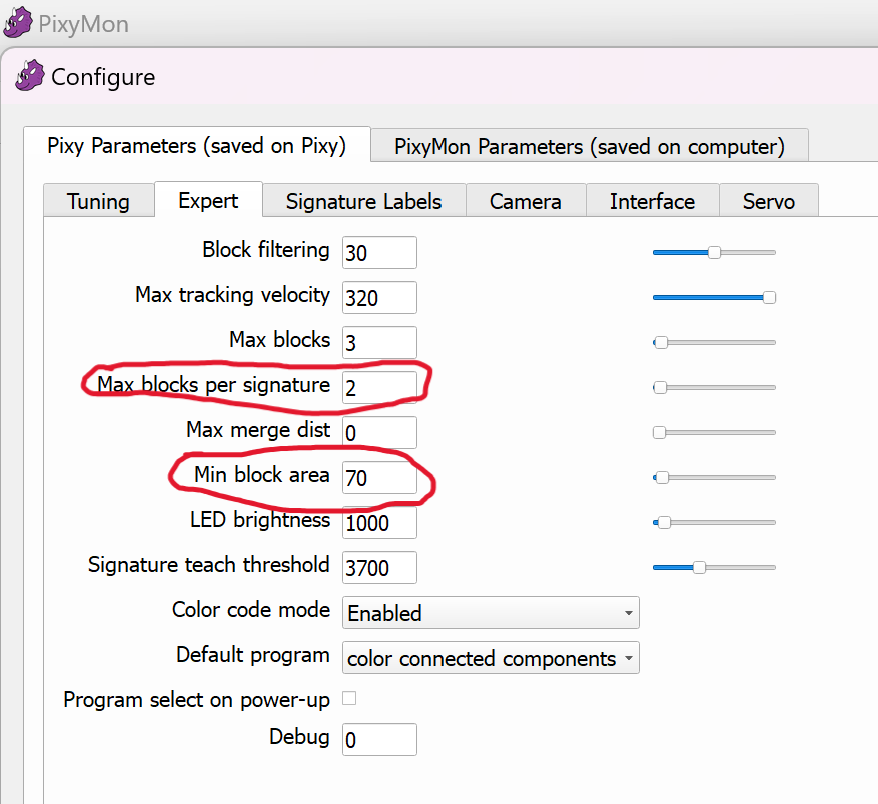
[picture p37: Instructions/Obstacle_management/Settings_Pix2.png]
PixyMon settings
 
</th>
</tr>
</table>
Every Pixy2 camera is unique, so the parameters that we have can be not relative to any other pixy2 camera. Also, the parameters need to be changed in different lighting conditions.

To set the pixy we click to "action" panel and "set signature" mode.

The main parameters of the Pixymon are signature range, camera brightness, max blocks, max blocks per signature, min block area. 

To view how Pixy2 camera track the block we click to "View" panel and then choose "blocks, video, detected pixels" mode. 

Also it is important to set "Block Filtering" to zero, and remove "Saturation" tick in "Camera" panel because it slows down block detection and worsense camera's tolerans to light changes
<table>
<tr>
<th width=800>
  
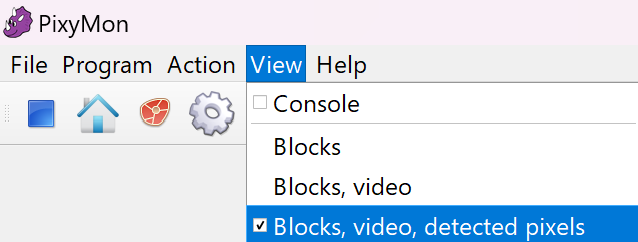
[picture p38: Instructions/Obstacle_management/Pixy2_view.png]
PixyMon view

</th>
</tr>
</table>

</br> </br>
Pixy2 is a camera that can detect and view colors of the objects and their relative position and size. It is a powerful tool for obstacle detection as it recognizes road signs and parking in the obstacle challenge. To set it you need to follow this steps:
1) Download Pixymon v2
2) Set the "camera brightness" in settings
3) Set the signatures in "Action" field
4) Set the "View" field to "blocks, video, detected pixels"
5) Regulate "signature range" for every signature you have
6) Regulate "min block area"

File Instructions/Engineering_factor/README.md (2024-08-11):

<div align = center style="display: flex; flex-direction: column; align-items: center; justify-content: center;">
  
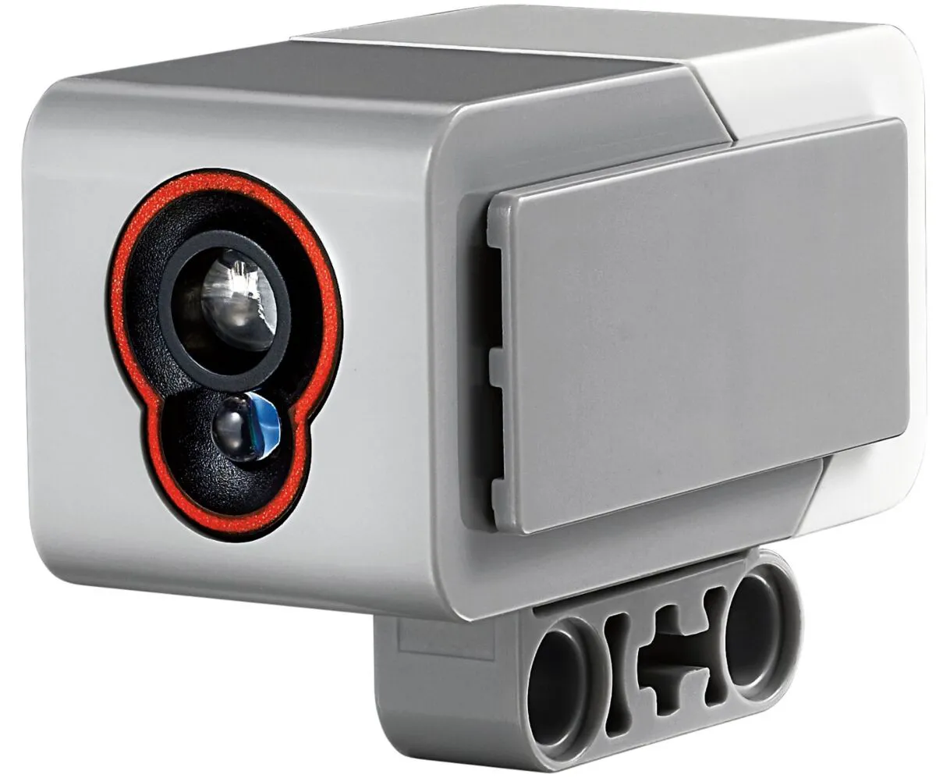
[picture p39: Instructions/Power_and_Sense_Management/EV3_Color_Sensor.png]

<p>Color Sensor</p>
<p>electroscheme: https://github.com/QZOFlameFE/FE2024_1st_repo_ByFlame/blob/main/schemes/95650%20Color%20sensor.pdf</p>

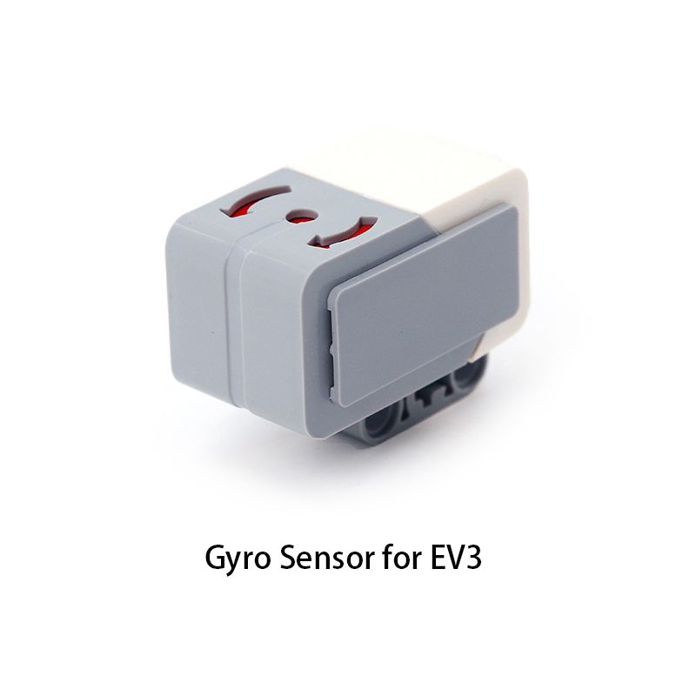
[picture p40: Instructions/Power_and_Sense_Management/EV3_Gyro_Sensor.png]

<p>Gyro Sensor</p>
<p>electroscheme: https://github.com/QZOFlameFE/FE2024_1st_repo_ByFlame/blob/main/schemes/99380%20Gyro%20sensor.pdf</p>

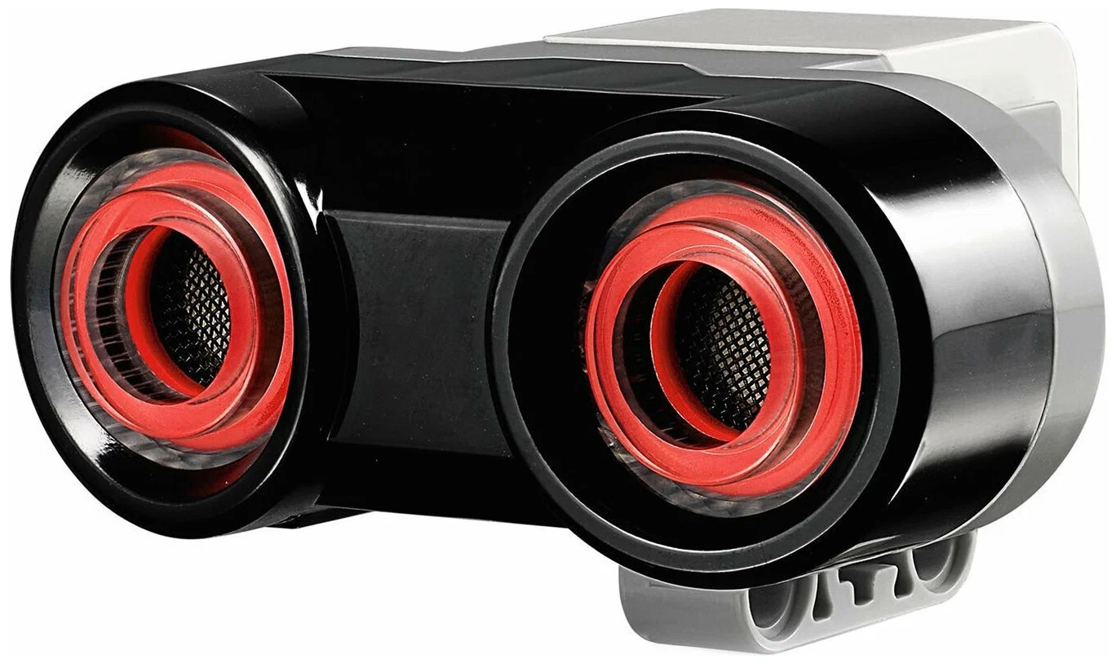
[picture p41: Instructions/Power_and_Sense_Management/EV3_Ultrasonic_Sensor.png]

<p>Ultrasonic Sensor</p>
<p>electroscheme: https://github.com/QZOFlameFE/FE2024_1st_repo_ByFlame/blob/main/schemes/95652%20Ultrasonic%20sensor.pdf</p>

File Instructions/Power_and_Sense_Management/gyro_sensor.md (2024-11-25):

<div align = center style="display: flex; flex-direction: column; align-items: center; justify-content: center;">

Color Sensor
<p>EV3 Gyro Sensor(Serial Number: 45505-1)</p>
<p>electroscheme: <a href="https://github.com/QZOFlameFE/FE2024_1st_repo_ByFlame/blob/main/schemes/99380%20Gyro%20sensor.pdf">https://github.com/QZOFlameFE/FE2024_1st_repo_ByFlame/blob/main/schemes/99380%20Gyro%20sensor.pdf</a> </p> 
<p>Gyro sensor LEGO MINDSTORMS block instruction: <a href="https://ev3-help-online.api.education.lego.com/Education/en-us/page.html?Path=blocks%2FLEGO%2FGyro.html">https://ev3-help-online.api.education.lego.com/Education/en-us/page.html?Path=blocks%2FLEGO%2FGyro.html</a> </p>
</div>
We use gyro sensor to save robot's initial(starting) position and count its deviation in degrees. Its features for precise angular motion detection and orientation measurement. Its key characteristics include angular velocity measurement, allowing real-time detection of rotational movement in degrees per second (°/s), and cumulative angle tracking, which provides continuous and accurate measurement of changes in orientation. Its high responsiveness enables the detection of even minute rotational changes, making it suitable for applications requiring sensitivity to directional shifts. This sensor enables real-time data transmission and processing for advanced control algorithms.
In programm we use gyro sensor for tracing the robot position, and control the drive of the robot like turns and correction of the straight ride by PD and PID regulators. Especially it place specific role in steering control that is performed by PID regulator. The PD regulator traces robot's position in angles in comparison with robot's initial (starting) position.
</br>
Gyro sensor have a significant role in odometry, especially in math constructions when the angles are needed. Detailed information is in the <a href="https://github.com/QZOFlameFE/FE2024_1st_repo_ByFlame/blob/main/Instructions/Power_and_Sense_Management/odometry.md">odometry</a> section.

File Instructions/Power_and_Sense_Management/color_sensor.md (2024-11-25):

<div align = center style="display: flex; flex-direction: column; align-items: center; justify-content: center;">

Color Sensor
<p>EV3 Color Sensor(Serial Number: 45506-1)</p>
<p>electroscheme: <a href="https://github.com/QZOFlameFE/FE2024_1st_repo_ByFlame/blob/main/schemes/95650%20Color%20sensor.pdf">https://github.com/QZOFlameFE/FE2024_1st_repo_ByFlame/blob/main/schemes/95650%20Color%20sensor.pdf</a> </p> 
<p>color sensor LEGO MINDSTORMS block instruction: <a href="https://ev3-help-online.api.education.lego.com/Education/en-us/page.html?Path=blocks%2FLEGO%2FColorSensor.html">https://ev3-help-online.api.education.lego.com/Education/en-us/page.html?Path=blocks%2FLEGO%2FColorSensor.html</a> </p>
</div>
The LEGO EV3 Color Sensor is a highly adaptable device designed for diverse applications in robotics. It can operate in three modes: color detection, ambient light measurement, and RGB mode, where it measures the intensity of red, green, and blue light. The RGB mode provides significant advantages by enabling the sensor to distinguish subtle variations in color, improving precision in color-based navigation. Its integration with the EV3 system simplifies data processing, while its ability to work in dynamic lighting conditions enhances versatility. EV3 Color Sensor balances functionality and ease of use. </br>
Color sensor is used to determine driving direction of the round and robot's position in corner section or in straightforward section. It detects orange and blue colors of the lines, if the first color that robot viewed is orange the direction is clockwise and vice versa if the color is blue the direction is anticlockwise. For this purposes we used color sensor's rgb mode, if the color is white rgb is near to 255, 255, 255; if the color is blue the red value needs to be less than 120, if the color is orange blue and green values sum and subtracted by 40 needs to be lower than value of red. 
</br>
Also we use color sensor to convert relative odometry to absolute odometry that is limited by map size. Detailed information is in the <a href="https://github.com/QZOFlameFE/FE2024_1st_repo_ByFlame/blob/main/Instructions/Power_and_Sense_Management/odometry.md">odometry</a> section.

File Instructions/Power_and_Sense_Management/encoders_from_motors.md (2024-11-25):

<div align = center style="display: flex; flex-direction: column; align-items: center; justify-content: center;">
<p>EV3 Encoders from motors(Serial Numbers: 45502-1, 4550-1)</p>
<p>electroscheme: <a href="https://github.com/QZOFlameFE/FE2024_1st_repo_ByFlame/blob/main/schemes/99455%20Medium%20motor.pdf">https://github.com/QZOFlameFE/FE2024_1st_repo_ByFlame/blob/main/schemes/95650%20Color%20sensor.pdf</a> </p> 
<p>Encoder LEGO MINDSTORMS block instruction: <a href="https://ev3-help-online.api.education.lego.com/Education/en-us/page.html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">https://ev3-help-online.api.education.lego.com/Education/en-us/page.html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</a> </p>
</div>
Encoders are used for calculating the distance that robot moved. The LEGO EV3 encoders, integrated within the motors, are significant for precise motion control. They measure shaft rotations in degrees and rotations, offering real-time feedback essential for closed-loop systems like PID controllers. This ensures accurate distance tracking, speed regulation, and smooth directional changes. Compared to optical encoders, which provide higher resolution but require external mounting, and magnetic encoders, known for robustness in harsh environments, LEGO encoders prioritize simplicity, reliability and integration. </br>

In programm they are used to know if the robot is in finish zone. They play significant role in driving and the steering control. PID regulator works by the encoder of steering. Also before the start robot fixes it steering for making perfect initial position as it is important for odometry.
</br>
The odometry is based on encoders in combine with gyro sensor. Detailed information is in the <a href="https://github.com/QZOFlameFE/FE2024_1st_repo_ByFlame/blob/main/Instructions/Power_and_Sense_Management/odometry.md">odometry</a> section.

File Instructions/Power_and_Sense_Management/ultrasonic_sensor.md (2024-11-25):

<div align = center style="display: flex; flex-direction: column; align-items: center; justify-content: center;">

Ultrasonic Sensor
<p>EV3 Ultrasonic Sensor(Serial Number: 45504-1)</p>
<p>electroscheme: <a href="https://github.com/QZOFlameFE/FE2024_1st_repo_ByFlame/blob/main/schemes/95652%20Ultrasonic%20sensor.pdf">https://github.com/QZOFlameFE/FE2024_1st_repo_ByFlame/blob/main/schemes/95652%20Ultrasonic%20sensor.pdf</a> </p> 
<p>Ultrasonic sensor LEGO MINDSTORMS block instruction: <a href="https://ev3-help-online.api.education.lego.com/Education/en-us/page.html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">https://ev3-help-online.api.education.lego.com/Education/en-us/page.html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</a> </p>
</div>
Ultrasonic sensor is used to determine relative odometry as it counts the distance between robot and the wall.
</br>
Ultrasonic is used to correct odometry, as it in combine with gyro can count the position of the robot in the road width and the distance between 2 walls by the odometry. Detailed information is in the <a href="https://github.com/QZOFlameFE/FE2024_1st_repo_ByFlame/blob/main/Instructions/Power_and_Sense_Management/odometry.md">odometry</a> section.

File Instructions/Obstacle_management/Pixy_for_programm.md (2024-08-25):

Pixy2 camera is a universal tool as it can work with EV3, arduino and raspberry. </br>
For the work in LEGO MINDSTORMS application you need to install "pixy block".
This block outputs: </br>
Signature id with the highest value of y coordinate </br>
camera's relative x coordinate of the object </br>
camera's relative y coordinate of the object </br>
relative width of the object </br>
relative height of the object </br>
angle of the object to camera </br>
<table>
<tr>
<th width=400>
  
Pixy2 block
</th>
</tr>
</table>

## Change of the driving direction
We use relative Y coordinate to detect if the last signature is green or red. If the robot views siqnature and it's y coordinate is high it is saved in variable named "last sign". 
## Parking position
To know where the parking is we also use pixy2 relative coordinates and odometry to know the parking zone's position.
## Bypassing obstacles
We use steering mechanism and pixy2 coordinates and connect them with linear function. So if the laps are close to robot linear function gives high values to steering mechanism's motor.

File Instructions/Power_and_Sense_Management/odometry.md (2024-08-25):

The Odomoetry is based in combine of all of the sensors that robot have. Ultrasonic measures distance to wall, gyro measures angle for math calculations, encoders measures the distance that robot moved, color sensor by specific math operations converts relative odometry to absolute odometry of the map.
# Relative Odometry
  Relative odometry is calculated by initial distance between robot and wall that measures by Ultrasonic sensor. That value is saved to variable named "fogX" and then, when the robot starts to move, encoders save the values of the distance that robot moved to the specific odometry loop that works in combine with gyro sensor. In this loop relatively previous value of the encoder is saved and compares with relatively current value of encoder and is substracted, lets name it "encoder change". The value that comes from gyro sensor lets name it "gyro angle" and the variable "gyro zero" that is the value that changes every time when robot turns. Number of turns named "Turn number" are calculated when the color sensor views a line, especially it counts only orange line numbers if the direction is clockwise and only blue line numbers if the direction is anticlockwise. "Gyro zero" is calculated like this: ["Turns number" * 90]. Then for comfortable calculations of odometry "gyro zero" substracts from "gyro angle". Now we can turn to odometry, the main formula for odometry is [("encoder change" * {sin or cos}("gyro angle" - "gyro zero"))/6.0770044]. 
  
## Explanation of the formula
  6.0770044 value comes from converting encoder's degrees and gear's cogs to centimeters. </br>
  the cos or sin is used for determinig x and y coordinates.
<table>
  <tr>
    <th width=400>

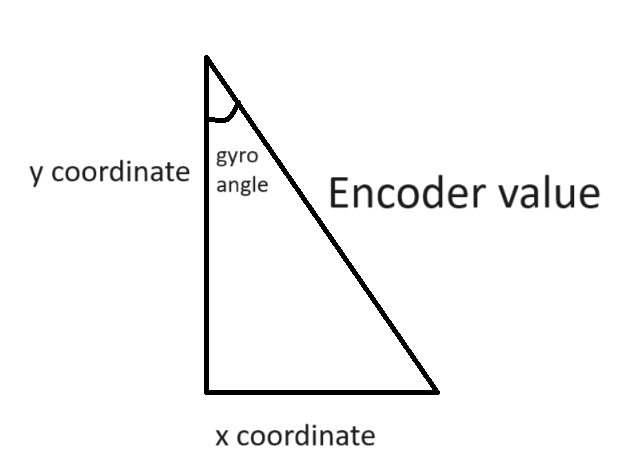
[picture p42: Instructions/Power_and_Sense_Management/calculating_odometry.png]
odometry explanation
   </br>
    </th>
  </tr>
</table>
<table>
  <tr>
    <th height=300>
    
  relative odometry programm part </br>
    </th>
  </tr>
  <tr>
    <th>
      
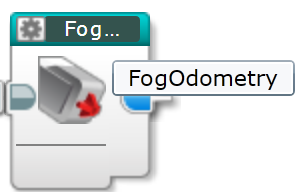
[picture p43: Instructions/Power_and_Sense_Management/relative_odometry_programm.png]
relative odometry in programm
   </br>
    </th>
  </tr>
</table>
</br>

# Absolute odometry
<table>
  <tr>
    <th width=1000>
      
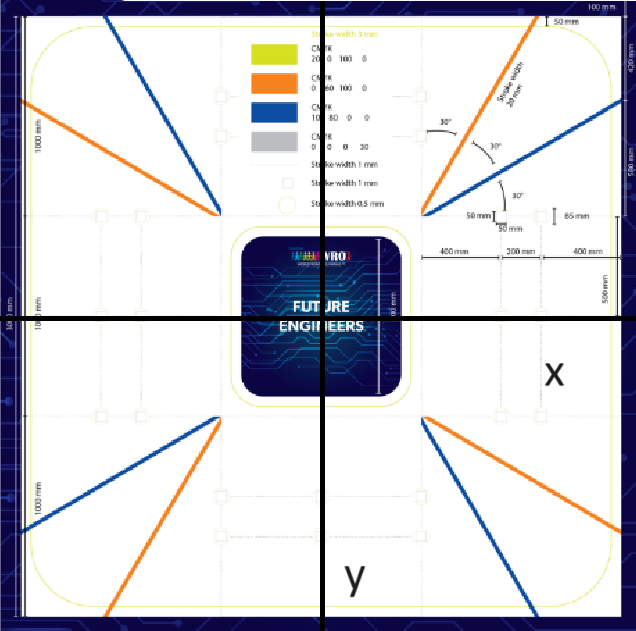
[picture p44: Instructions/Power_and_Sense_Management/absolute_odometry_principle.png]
absolute odometry principle
 </br>
> [!NOTE]
> this is our XY coordinates for odometry

  </th>
  </tr>
</table>

<table>
  <tr>
    <th width=200>
      
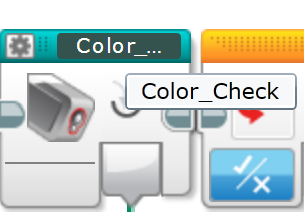
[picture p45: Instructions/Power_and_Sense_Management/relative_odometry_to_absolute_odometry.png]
relative odometry to absolute odometry
 
> [!NOTE]
> this is a part of programm where relative odometry transfers to absolute odometry

 </th>
  </tr>
</table>

<table>
  <tr>
    <th width=200>

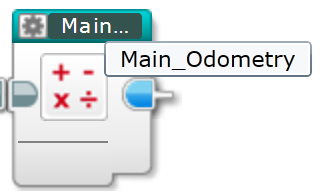
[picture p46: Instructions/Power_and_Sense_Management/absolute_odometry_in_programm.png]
absolute odometry in programm
 </br>
> [!NOTE]
> part of programm where absolute odometry compiles

 </th>
  </tr>
</table>
When color sensor detects the line relative odometry transfers to absolute odometry with  coordinates center in center of the map. The principle is the x coordinate of the relative odometry by specific math operations transfers to full odometry. When the driving direction is clockwise we substract 100 from relative odometry's X coordinate and by linear function of the orange line in the map we transfer relative odometry to absolute odometry. If the driving direction is anticlockwise we sum 100 with relative odometry's X coordinate and with linear function of the blue line of the map we get absolute odometry.

## Usage of odometry in programm
### Aligning robot to the center
<table>
  <tr>
    <th width=200>

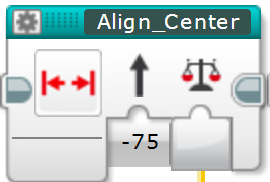
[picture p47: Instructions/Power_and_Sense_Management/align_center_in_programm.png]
align_center_in_programm

</th>
</tr>
</table>
To align robot to the center of the straightforward zone. It is great to aligning robot to the center of the road for the Pixy2 camera to attach better view. 
### Avoid crash
<table>
<tr>
<th width=200>

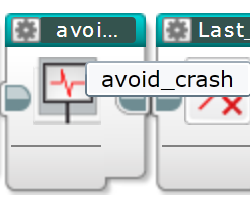
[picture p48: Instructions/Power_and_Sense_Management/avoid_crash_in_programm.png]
avoid crash in programm

</th>
</tr>
</table>
Also we use odometry to detect the coordinates of pillars (red and green signs). If robot is too close to the pillars odometry helps to avoid accident and robot by gyro sensor and specific programm robot moves to the back. it works only between corner and straightforward zones to avoid collision with pillars in the back of the robot.
# Aligning odometry
<table>
  <tr>
    <th width=200>
      
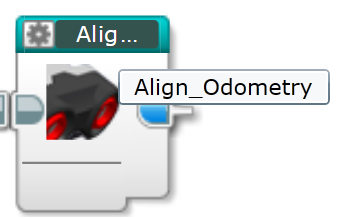
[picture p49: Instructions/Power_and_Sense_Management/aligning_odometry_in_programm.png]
aligning odometry in the programm

    </th>
  </tr>
</table>
Odometry is a complex principle that can lose its accuracy over time, therefore, in order for our odometry to be accurate, we correct it with the help of ultrasonic and gyro sensor.

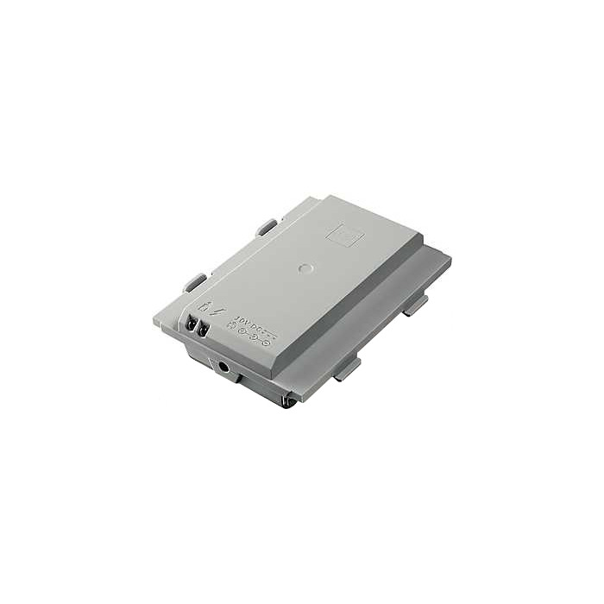
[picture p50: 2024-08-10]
Instructions/Power_and_Sense_Management/EV3_Rechargable_10V_Lithuim_Battery.png

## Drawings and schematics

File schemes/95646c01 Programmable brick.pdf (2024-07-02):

# Ram Flash

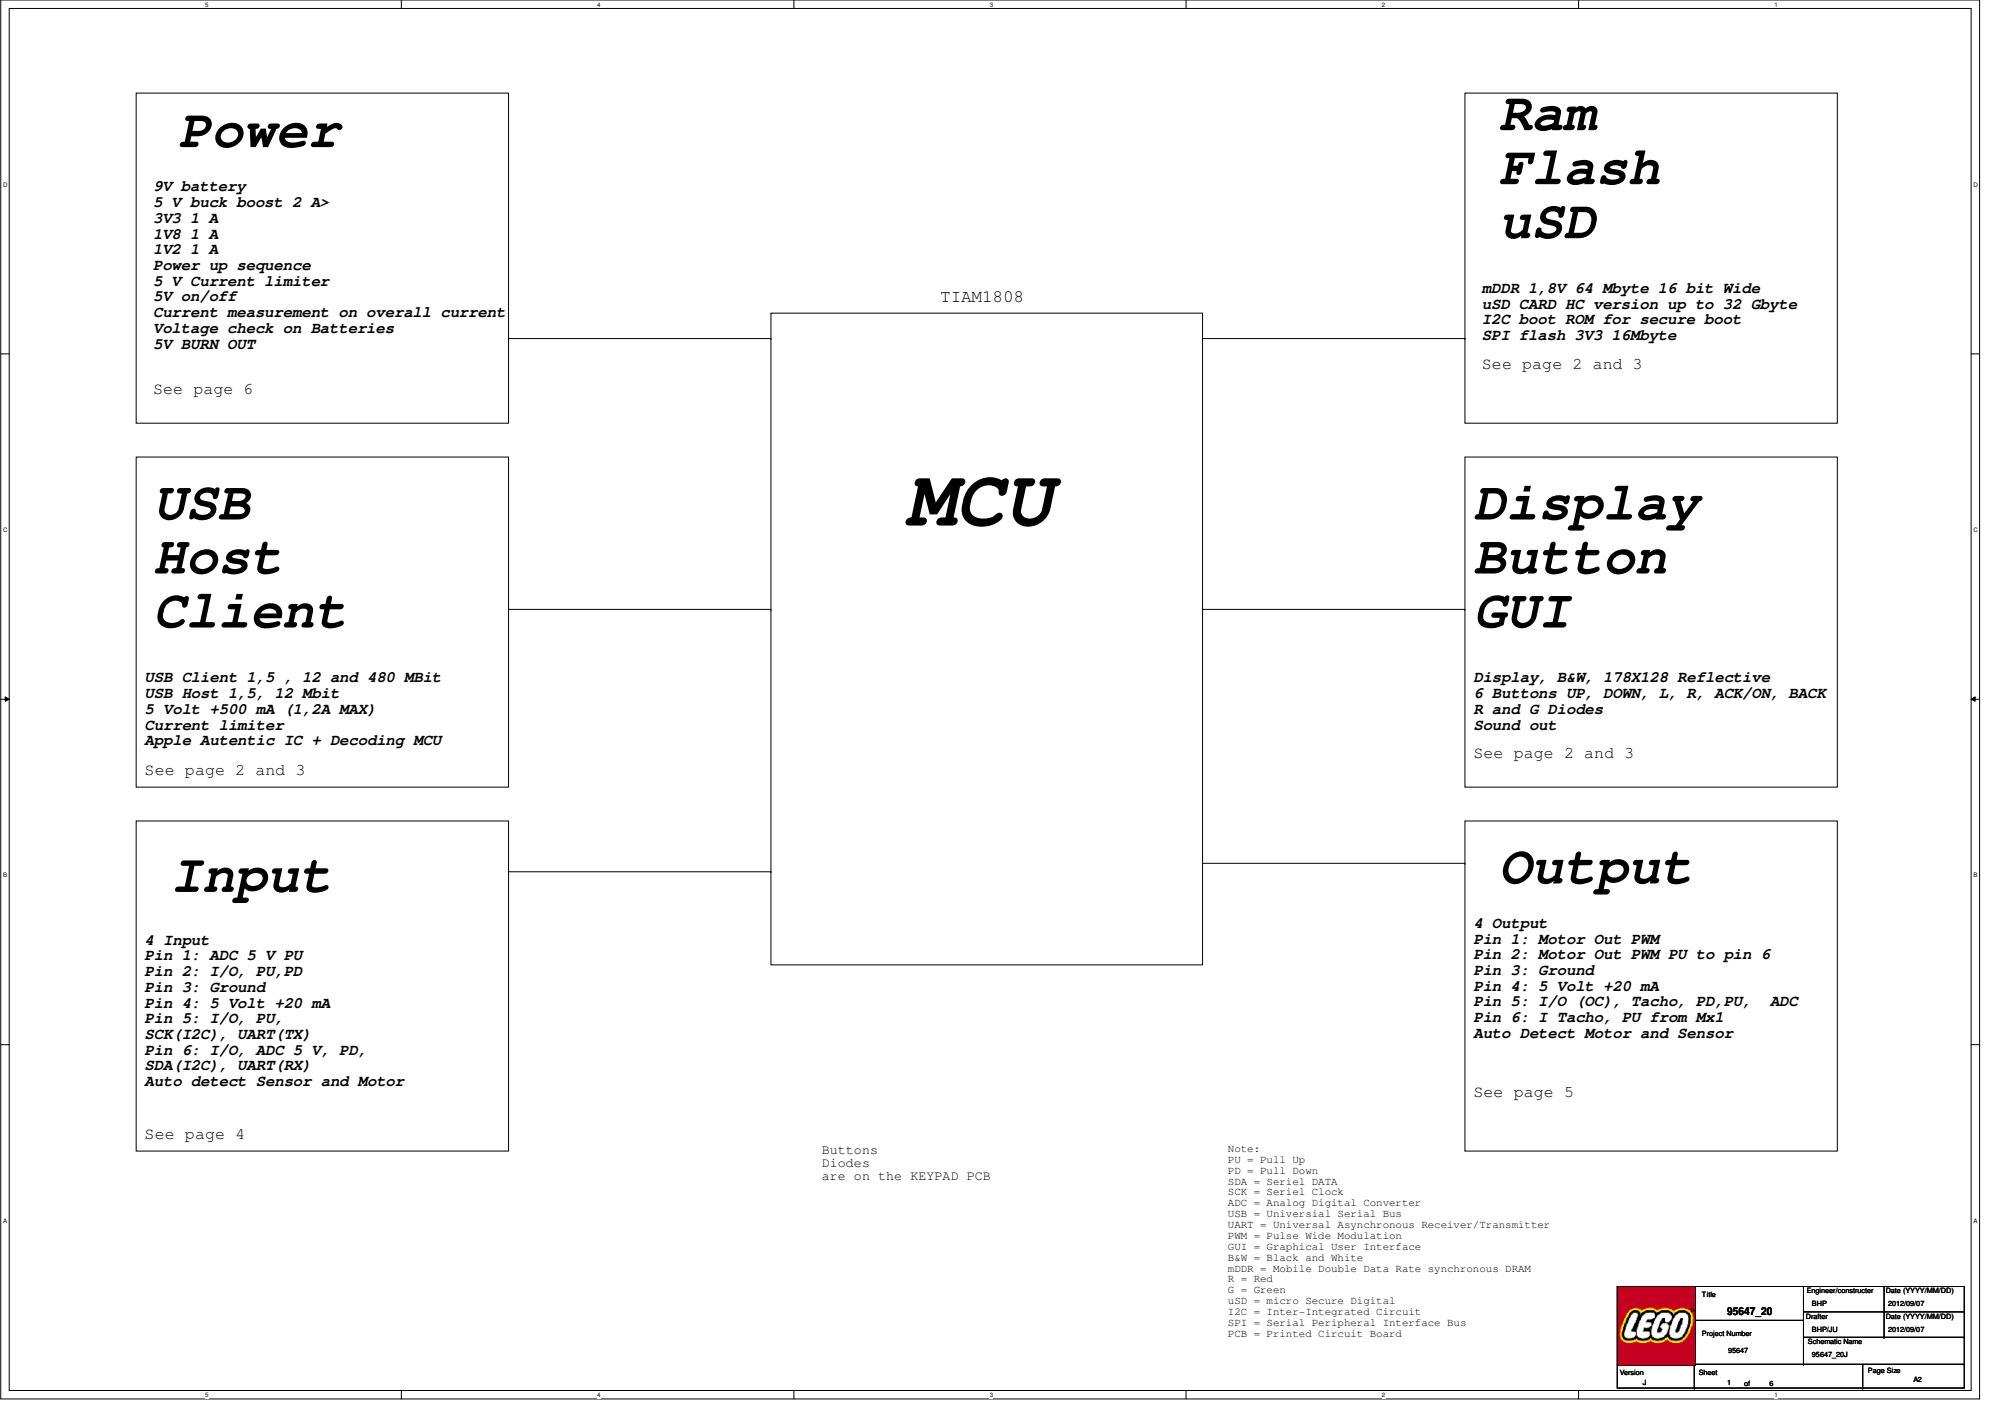
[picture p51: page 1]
MCU; uSD; Display Button GUI; Output; Power; USB Host Client; Pin 5: I/O (OC), Tacho, PD,PU,; ADC; TIAM1808; See page 6; See page 4; See page 5; Title; Project Number; Engineer/constructer; Schematic Name; Drafter; Date (YYYY/MM/DD); Version; Sheet; Page Size; BHP; BHP/JU

9V battery
5 V buck boost 2 A>
Power up sequence
5 V Current limiter
5V on/off
Current measurement on overall current
Voltage check on Batteries
5V BURN OUT

mDDR 1,8V 64 Mbyte 16 bit Wide
uSD CARD HC version up to 32 Gbyte
I2C boot ROM for secure boot
SPI flash 3V3 16Mbyte

See page 2 and 3

USB Client 1,5 , 12 and 480 MBit
USB Host 1,5, 12 Mbit
5 Volt +500 mA (1,2A MAX)
Current limiter
Apple Autentic IC + Decoding MCU

Display, B&W, 178X128 Reflective
6 Buttons UP, DOWN, L, R, ACK/ON, BACK
R and G Diodes
Sound out

Input

4 Output
Pin 1: Motor Out PWM
Pin 2: Motor Out PWM PU to pin 6
Pin 3: Ground
Pin 4: 5 Volt +20 mA
Pin 6: I Tacho, PU from Mx1
Auto Detect Motor and Sensor

4 Input
Pin 1: ADC 5 V PU
Pin 2: I/O, PU,PD
Pin 5: I/O, PU,
SCK(I2C), UART(TX)
Pin 6: I/O, ADC 5 V, PD,
SDA(I2C), UART(RX)
Auto detect Sensor and Motor

Buttons
Diodes
are on the KEYPAD PCB

Note:
PU = Pull Up
PD = Pull Down
SDA = Seriel DATA
SCK = Seriel Clock
ADC = Analog Digital Converter
USB = Universial Serial Bus
UART = Universal Asynchronous Receiver/Transmitter
PWM = Pulse Wide Modulation
GUI = Graphical User Interface
B&W = Black and White
mDDR = Mobile Double Data Rate synchronous DRAM
R = Red
G = Green
uSD = micro Secure Digital
I2C = Inter-Integrated Circuit
SPI = Serial Peripheral Interface Bus
PCB = Printed Circuit Board

Date (YYYY/MM/DD)

D

D

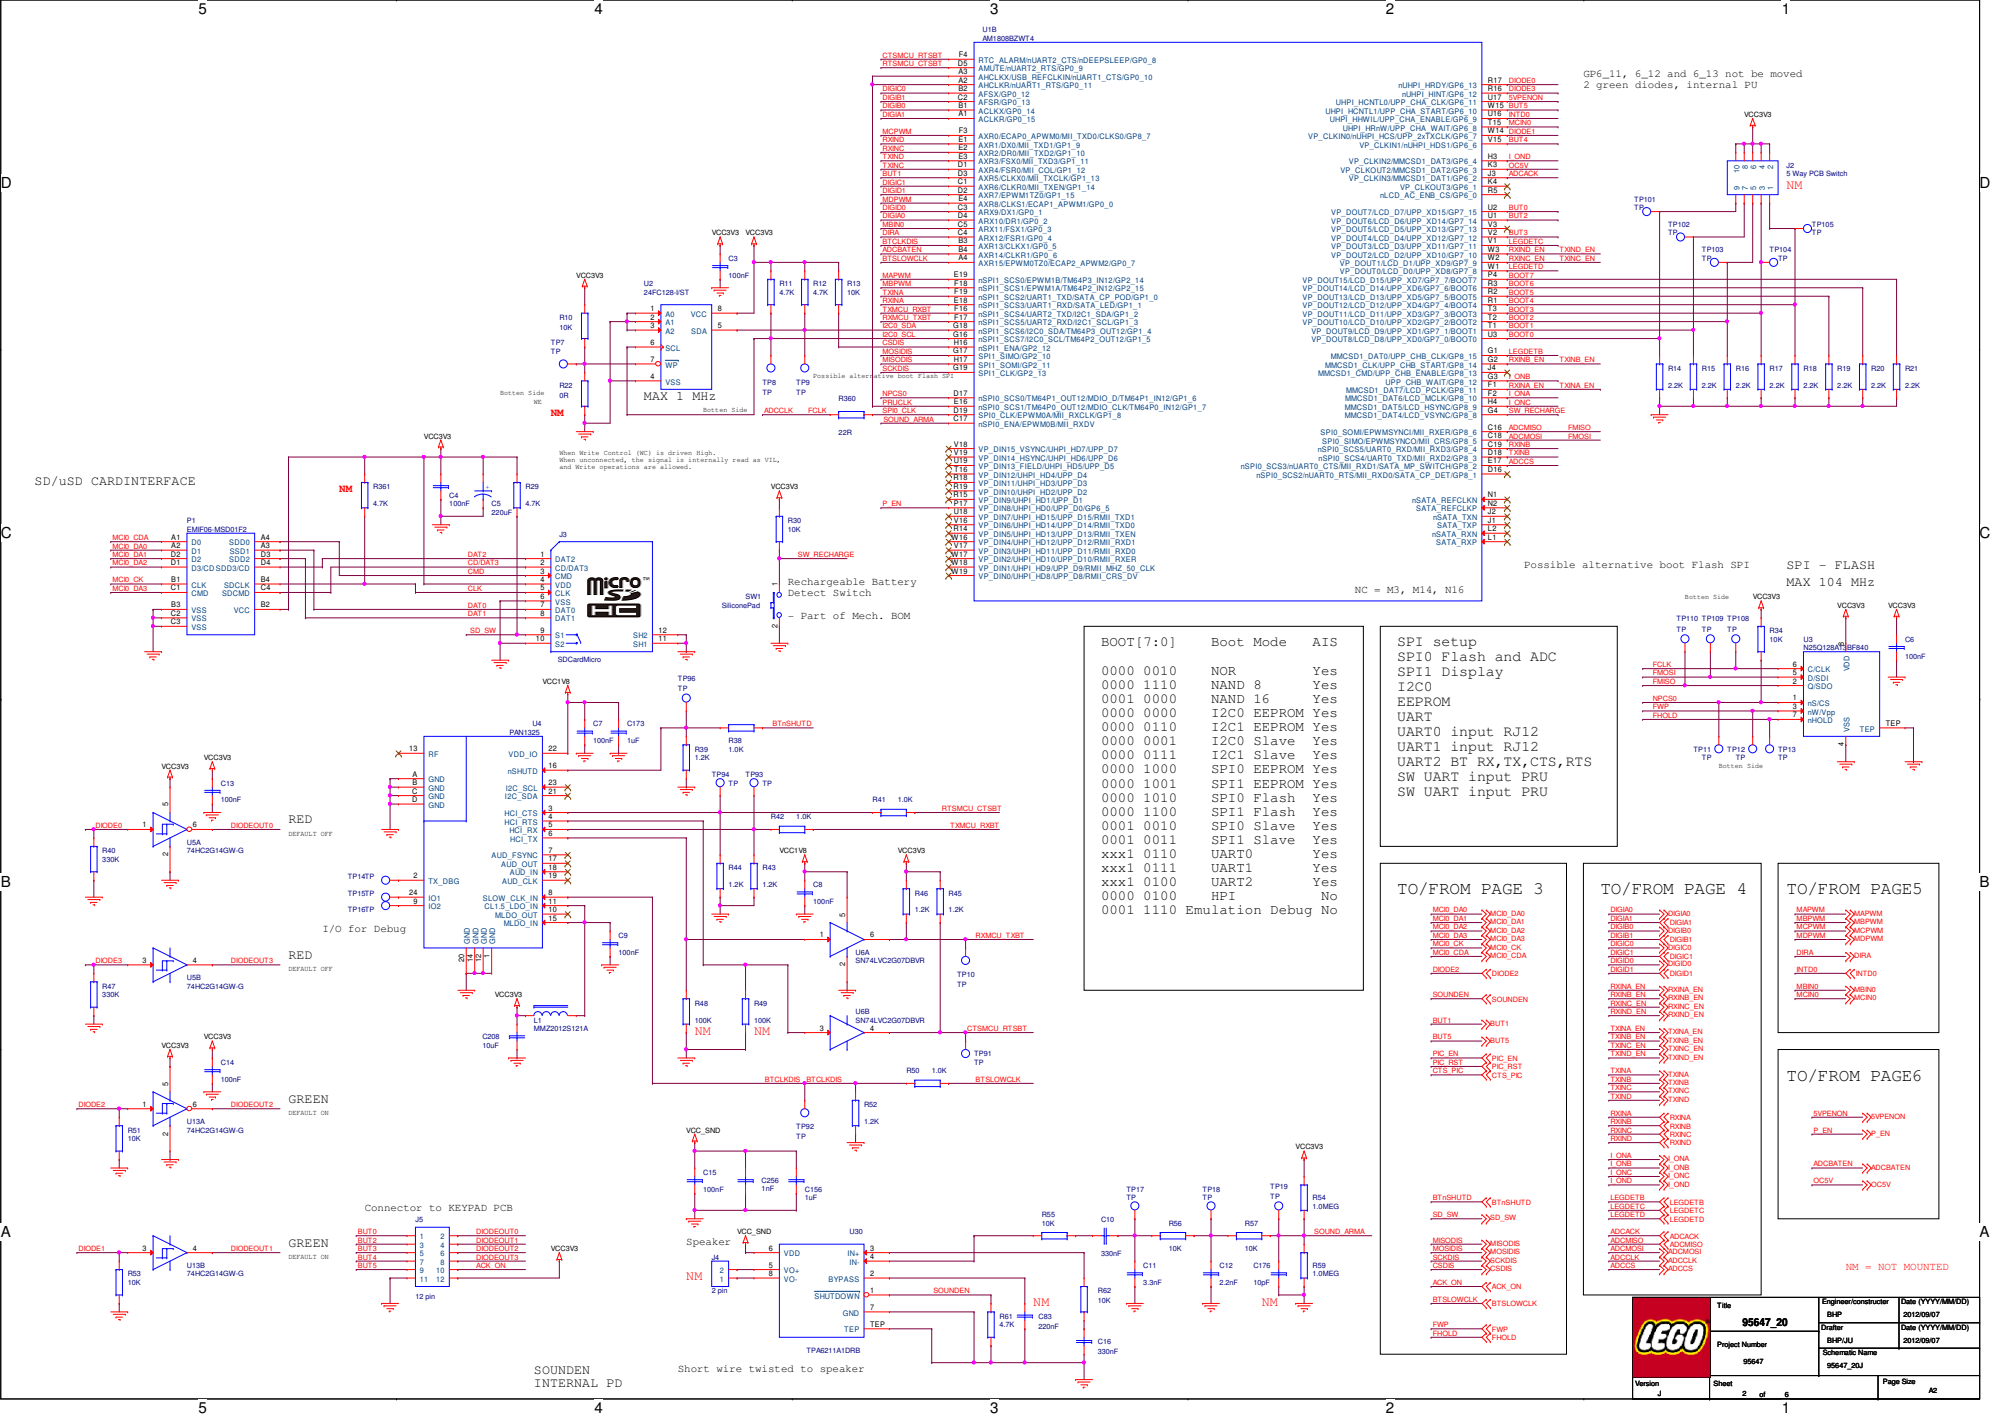
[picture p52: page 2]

GP6_11, 6_12 and 6_13 not be moved
2 green diodes, internal PU

Possible alternative boot Flash SPI

When Write Control (WC) is driven High.
When unconnected, the signal is internally read as VIL,
and Write operations are allowed.

CMD | 3

- Part of Mech. BOM

SW UART input PRU

Connector to KEYPAD PCB

Short wire twisted to speaker

D

D

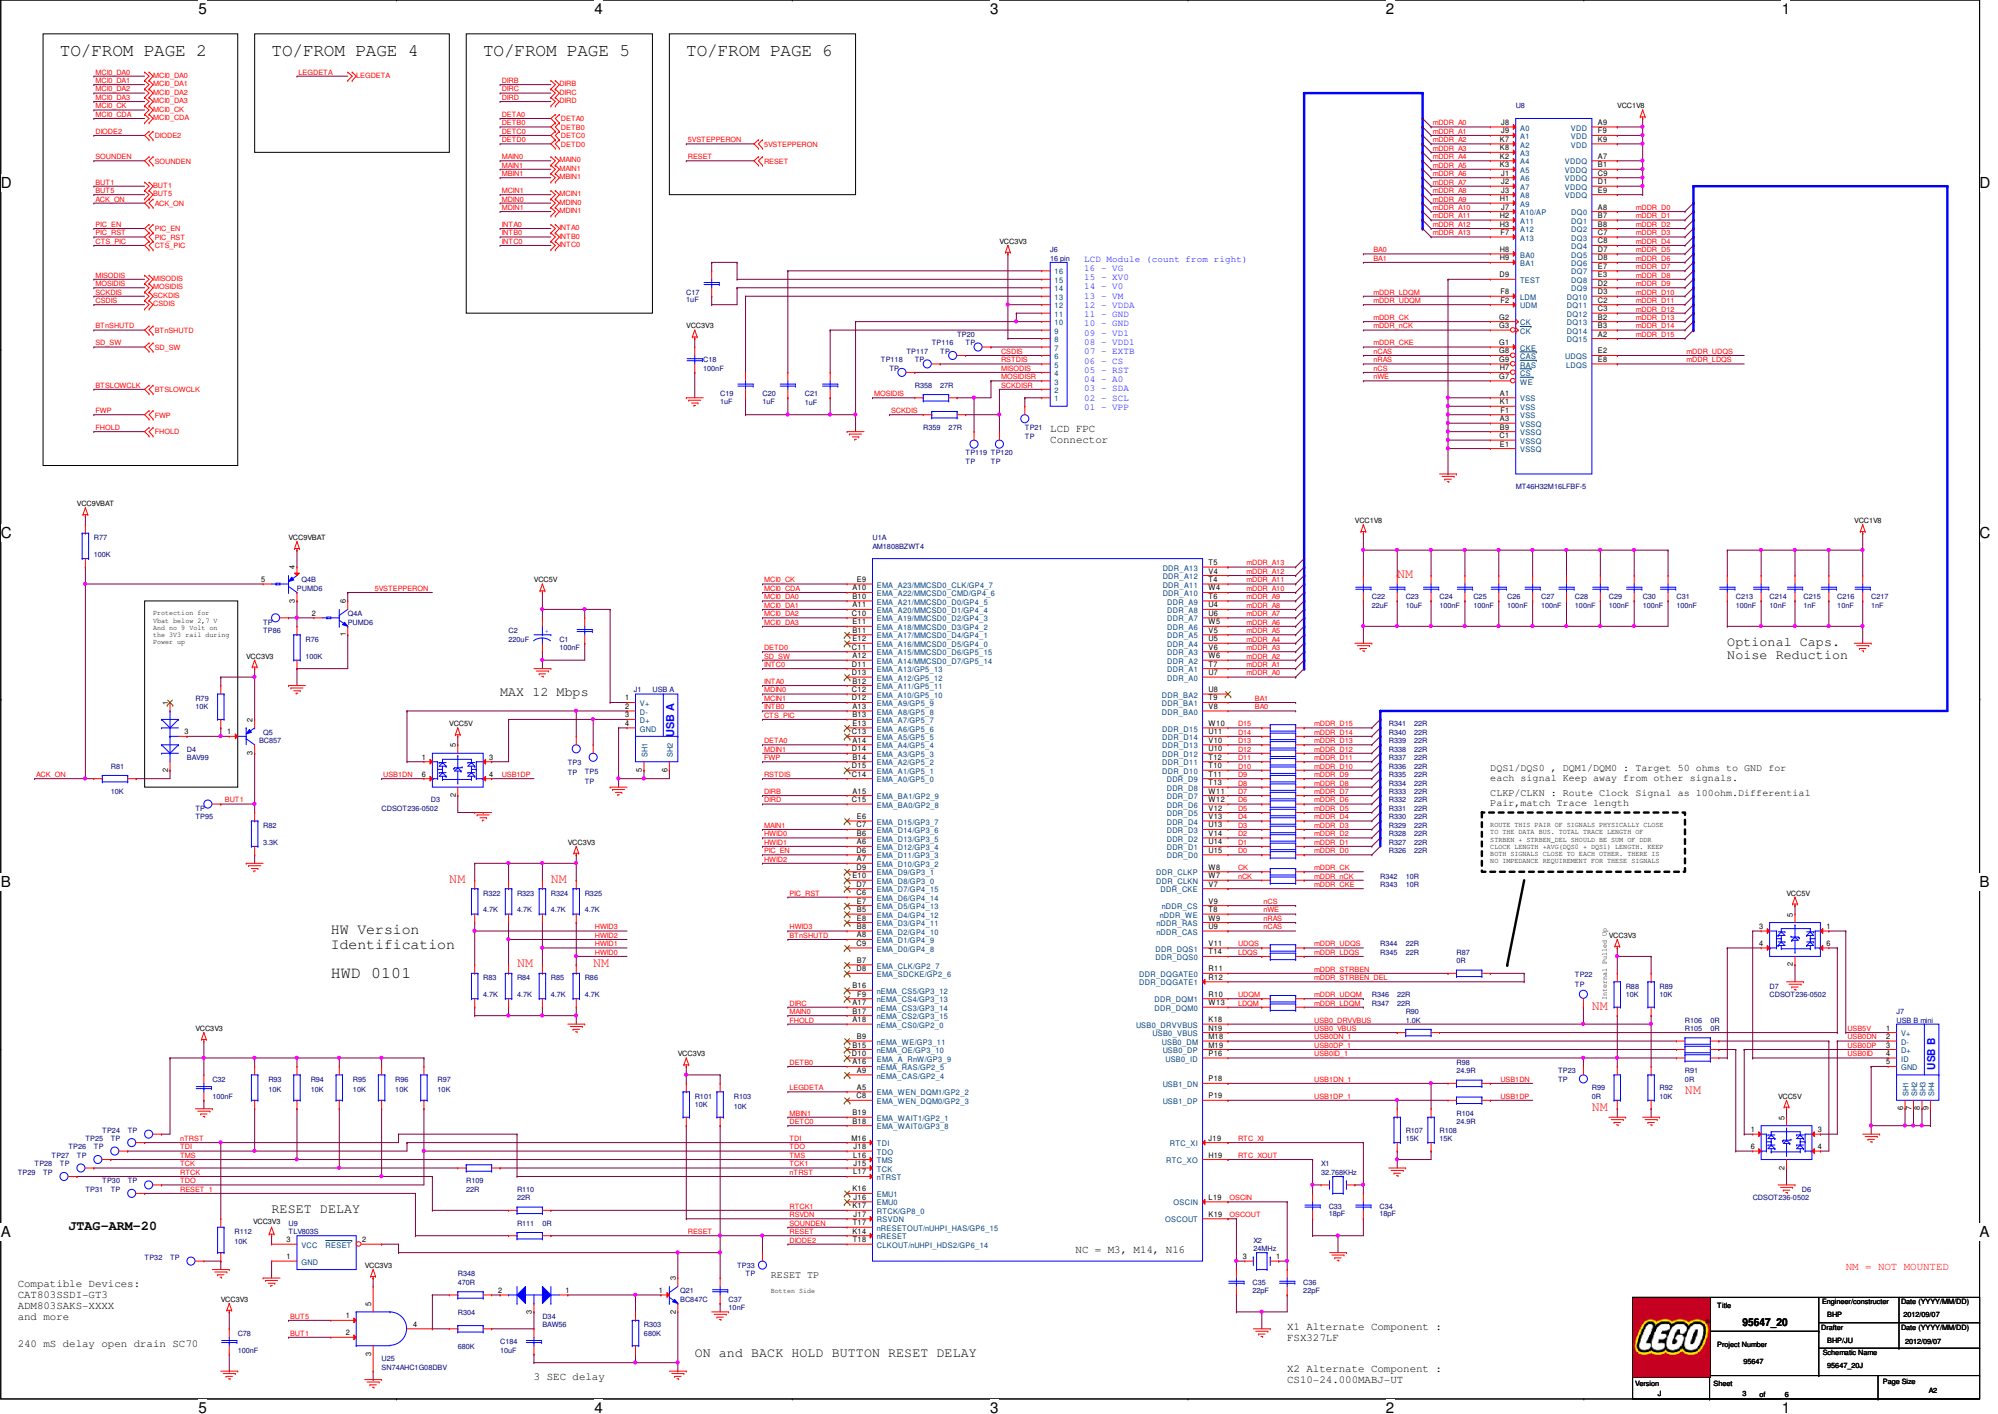
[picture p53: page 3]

Protection for
Vbat below 2,7 V
And no 9 Volt on
the 3V3 rail during
Power up

DQS1/DQS0 , DQM1/DQM0 : Target 50 ohms to GND for
each signal Keep away from other signals.
CLKP/CLKN : Route Clock Signal as 100ohm.Differential
Pair,match Trace length

ROUTE THIS PAIR OF SIGNALS PHYSICALLY CLOSE
TO THE DATA BUS. TOTAL TRACE LENGTH OF
STRBEN + STRBEN_DEL SHOULD BE SUM OF DDR
CLOCK LENGTH +AVG(DQS0 + DQS1) LENGTH. KEEP
BOTH SIGNALS CLOSE TO EACH OTHER. THERE IS
NO IMPEDANCE REQUIREMENT FOR THESE SIGNALS

240 mS delay open drain SC70

ON and BACK HOLD BUTTON RESET DELAY

D | D

# INPUT A

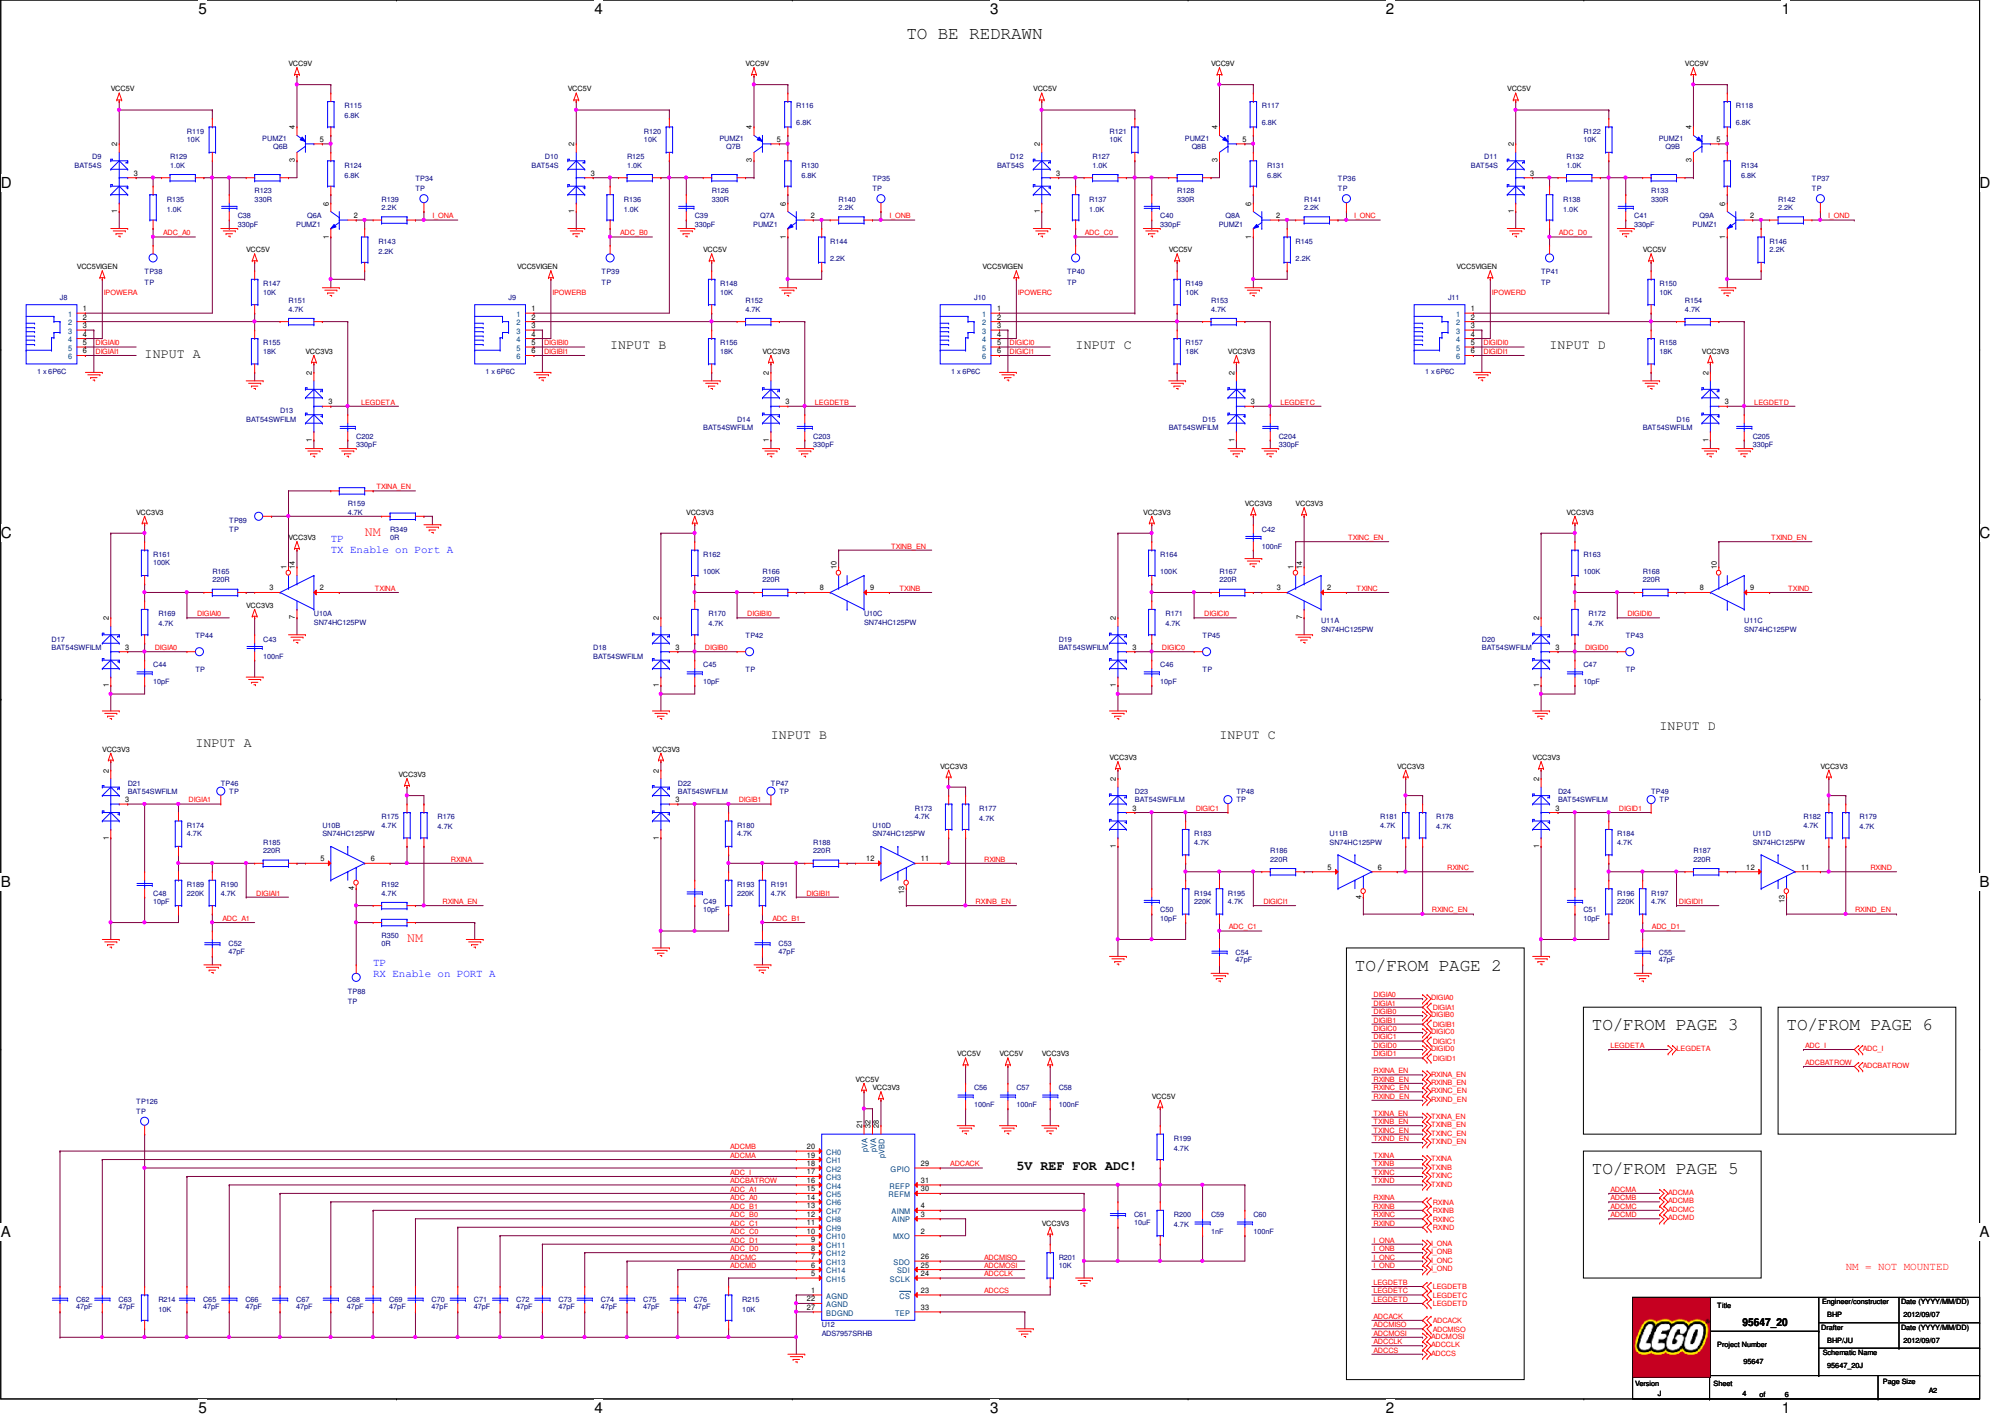
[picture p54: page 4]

TX Enable on Port A

## MotorA

## MotorB

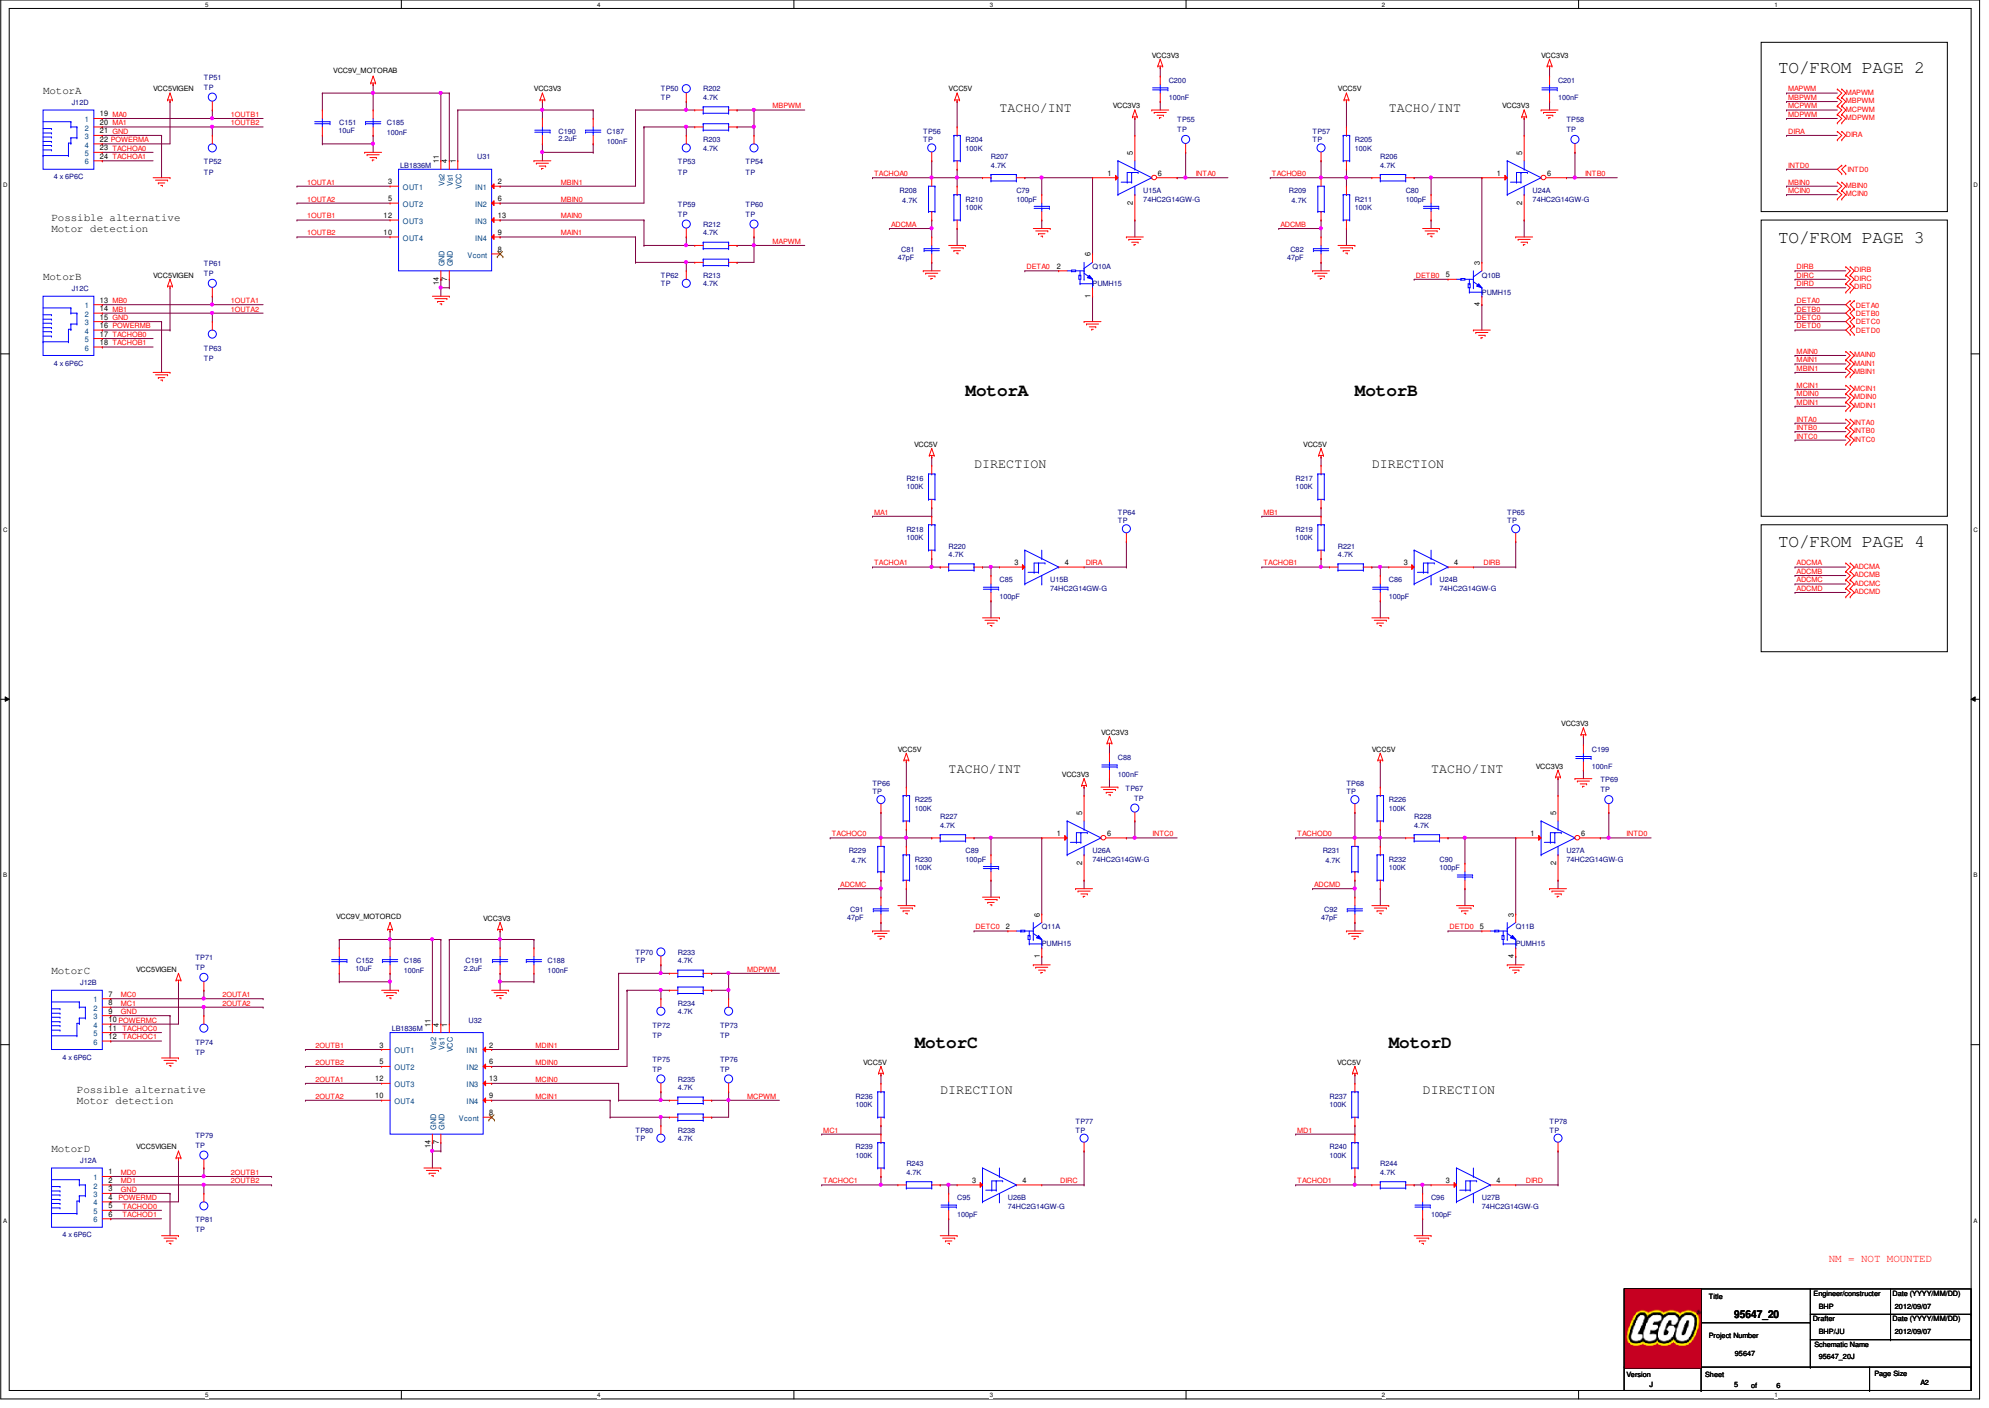
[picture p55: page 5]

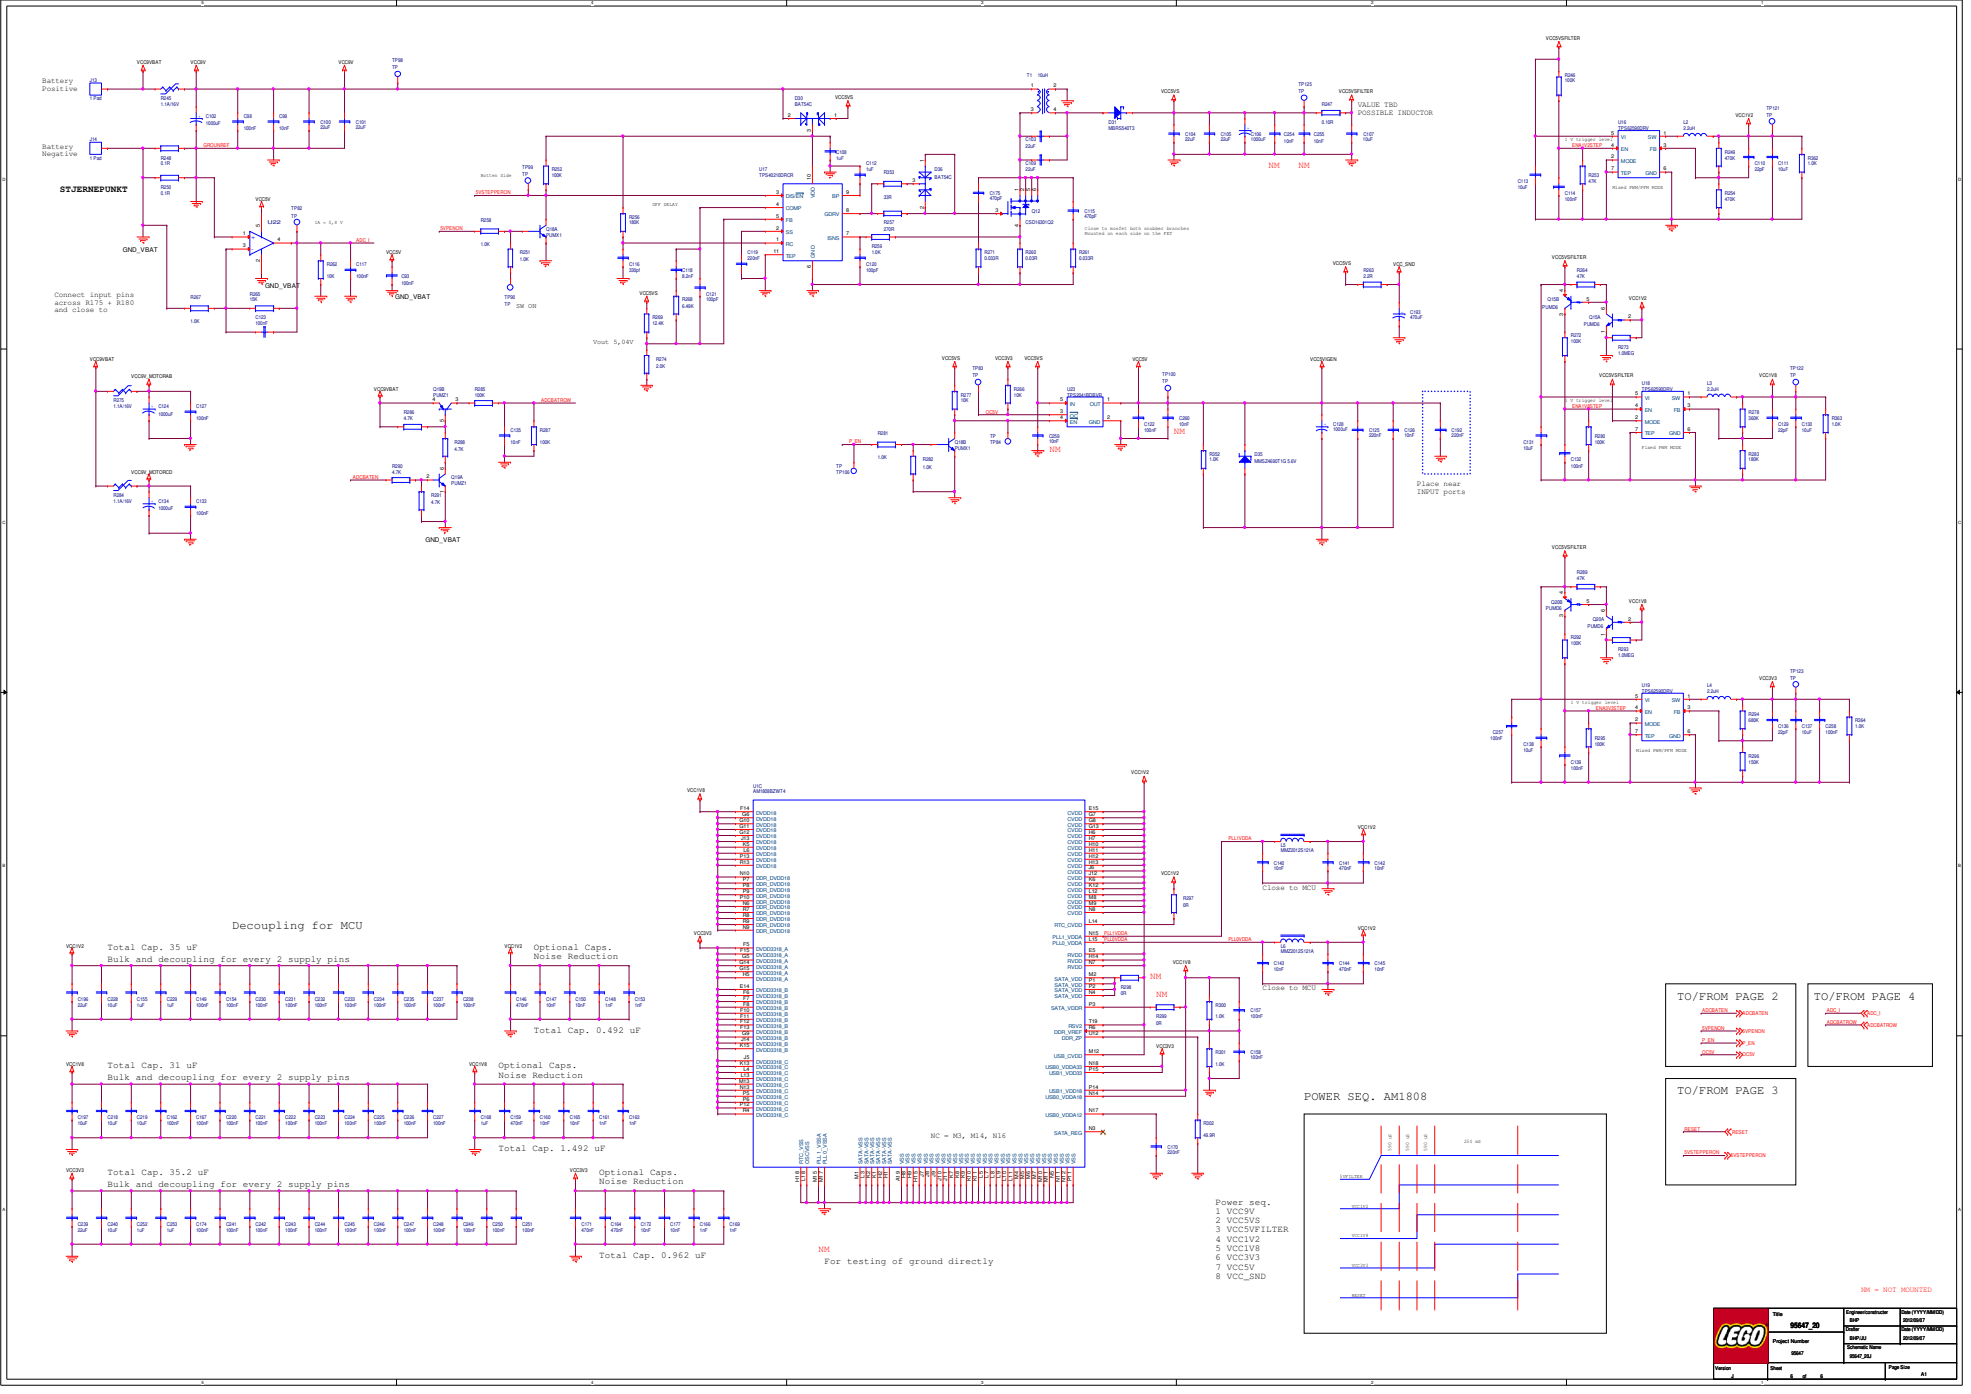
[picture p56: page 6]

Mixed PWM/PFM MODE

Close to mosfet both snubber branches
Mounted on each side on the FET

Total Cap. 35 uF
Bulk and decoupling for every 2 supply pins

For testing of ground directly
